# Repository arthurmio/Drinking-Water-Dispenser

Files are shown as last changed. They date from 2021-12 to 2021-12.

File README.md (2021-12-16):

# Drinking Water Dispenser
The objective of the project is to build a paid water dispenser to fill 1L bottles.

This dispenser will be located on the roadside to allow hikers to recharge their bottle and thus reduce the use of plastic.

The project is developed by Mandor which is an ecological reserve located 4km from the village of Machu Picchu in Peru, 
possessing a botanical garden with a waterfall to discover the flora and fauna, a restaurant, accommodation and a campsite.

# Contact
Facebook / Instagram : @mandormachupicchu

Whatsapp : +51 940 188 155

<p align="center">
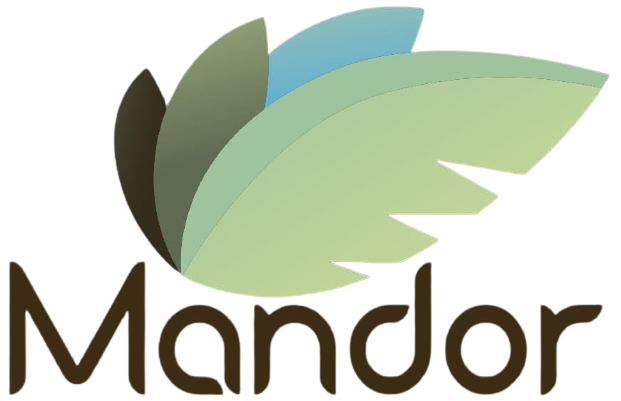
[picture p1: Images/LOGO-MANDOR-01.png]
mandor logo
  
</p>

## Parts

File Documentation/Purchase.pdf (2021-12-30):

Name | Component | Reference Naylamp | Price (soles) | Url
Coin Acceptor Selector de monedas CH-926 #SKU: 000373 140 https://naylampmechatronics.com/sensores/373-selector-de-monedas.html
Flow Meter Sensor de flujo de agua 1/2" YF-S201 #SKU: 000108 20 https://naylampmechatronics.com/sensores-liquido/108-sensor-de-flujo-de-agua-12-yf-s201.html

Solenoid Valve Válvula solenoide 1/2" 12VDC #SKU: 000314 25 https://naylampmechatronics.com/valvulas/314-valvula-solenoide-1p2-pulg-12vdc.html

Button Pulsador con cubierta #SKU: 000211 1 https://naylampmechatronics.com/accesorios-y-prototipado/211-pulsador-con-cubierta-para-kit.html

Arduino Arduino Nano Every with Headers / 61 https://store-usa.arduino.cc/collections/boards?sort_by=price-ascending

Relay or Transistor 12V DRIVER MOSFET IRF520 6A #SKU: 000239 6 https://naylampmechatronics.com/drivers/239-driver-mosfet-irf520-6a.html
DC-DC Converter Convertidor Voltaje DC-DC Step-Up 2A MT3608 #SKU: 000119 15 https://naylampmechatronics.com/conversores-dc-dc/119-convertidor-voltaje-dc-dc-step-up-2a-mt3608.html
/!\ Complementary material Resistance Capacity Led Cables BreadBoard Multimeter Arduino Alimentation | TOTAL 268

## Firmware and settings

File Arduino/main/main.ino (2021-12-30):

//////////////////////////////////////////////////////////////////////////
/// Name        : main.ino
/// Description : Principal code for drinking water dispenser
/// Author      : Arthur MARIANO
/// Github      : https://github.com/arthurmio/Drinking-Water-Dispenser
/// Date        : 27/12/2021
//////////////////////////////////////////////////////////////////////////

#include <Arduino.h>
#include <Time.h>

///////////////////
// Instantiation //
///////////////////

// Time //
volatile float currentTime = 0.00;
volatile float lastTime = 0.00;
volatile float start = 0.00;
volatile float coinsValueSavedTime = 0.00;

// Flow Meter //
const int flowMeterPin = 2; // interrupt port
const float factorK = 7.5;
volatile int pulse_freq = 0 ;
volatile float flow = 0.00;
volatile float waterVolume = 0.00;
volatile float flowCounter = 0.00;

// Coin Acceptor //
const int coinAcceptorPin = 3; // interrupt port
volatile float coinsValue = 0.00;
volatile float coinsValueSaved = 0.00;
volatile float moneyValue = 0.00;
volatile bool payed = false;

// Solenoid //
const int solenoidPin = 4; 


///////////
// setup //
///////////
void setup() {
  pinMode(flowMeterPin, INPUT);
  pinMode(coinAcceptorPin, INPUT); 
  pinMode(solenoidPin, OUTPUT);
  Serial.begin(9600);
  attachInterrupt(digitalPinToInterrupt(flowMeterPin), pulseFlow, RISING);
  attachInterrupt(digitalPinToInterrupt(coinAcceptorPin), pulseMachine, RISING);
  currentTime = millis();
  lastTime = currentTime;
}


//////////
// loop //
//////////
void loop(){
  // money calcul
  currentTime = millis();
  if(currentTime <= (start+1000)){
    coinsValueSaved = coinsValue;
    coinsValueSavedTime = millis();
  }
  else{
    coinsValue = 0;
  }
  if(currentTime >= (coinsValueSavedTime+1000)){
    if(coinsValueSaved>=5 && coinsValueSaved <= 11){
      moneyValue = 1; // 0.50 sole
      solenoidOpen(moneyValue); 
    }
    else if(coinsValueSaved>11){
      moneyValue = 2; // 1 sole
      solenoidOpen(moneyValue);
    }
    else{
      moneyValue = 0; // no money
      solenoidOpen(moneyValue);
    }   
  }
  flowCounter=0.00;
  flow=0.00;
  pulse_freq=0.00;
  while(payed==true){
    currentTime = millis();
    if(currentTime >= (lastTime + 100)) // count always the flow every second 
    {   
      lastTime = currentTime; 
      flow = (pulse_freq / factorK) / 60; // flow in L/min
      pulse_freq = 0; // Reset Counter
      Serial.print(flow, DEC); 
      Serial.println(" L/Min");
      flowCounter = flowCounter + flow;
      Serial.print(flowCounter, DEC); 
      Serial.println(" L");
      flowCount(moneyValue, flowCounter);
      digitalWrite(solenoidPin, LOW); // solenoid open
    }
  }
  digitalWrite(solenoidPin, HIGH); // solenoid closed
}

///////////////
// Functions //
///////////////

// Flow Meter //
void pulseFlow() // interrupt fonction for flow meter
{
  pulse_freq++;
}

void flowCount(int moneyValue, float flowCounter){ // calcul for volume
  if(moneyValue == 1){
    if(flowCounter >= 0.50){
      payed = false;
      Serial.println("0.50L water served");
    }
  }
  else if(moneyValue == 2){
    if(flowCounter >= 0.97){
      payed = false;
      Serial.println("1L water served");
    }
  }
  coinsValueSaved=0;
}

// Coin Acceptor //
void pulseMachine(){ // interrupt fonction for coin acceptor
  coinsValue  = coinsValue + 0.5;
  start = millis();
}

// Solenoid //
void solenoidOpen(int moneyValue){
  if(moneyValue==1){ // 0.50sole
    payed = true;
  }
  else if(moneyValue==2){ // 1sole
    payed = true;
  }
  else
    payed = false;
}

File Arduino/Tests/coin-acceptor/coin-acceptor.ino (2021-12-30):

//////////////////////////////////////////////////////////////////////////
/// Name        : coin-acceptor.ino
/// Description : Code for testing the coin-acceptor CH-926
/// Author      : Arthur MARIANO
/// Github      : https://github.com/arthurmio/Drinking-Water-Dispenser
/// Date        : 30/12/2021
//////////////////////////////////////////////////////////////////////////
#include <Arduino.h>
#include <Time.h>

//Time
volatile float currentTime = 0.00;
volatile float lastTime = 0.00;
volatile float start = 0.00;
volatile float coinsValueSavedTime = 0.00;

const int coinAcceptorPin = 3;
volatile float coinsValue = 0.00;
volatile float coinsValueSaved = 0.00;


void setup() {
  pinMode(coinAcceptorPin, INPUT); 
  Serial.begin(9600);
  attachInterrupt(digitalPinToInterrupt(coinAcceptorPin), pulseMachine, RISING);
  
}

void loop() {
  currentTime = millis();
  if(currentTime <= (start+1000)){
    coinsValueSaved = coinsValue;
    coinsValueSavedTime = millis();
  }
  else{
    coinsValue = 0;
  }
  if(currentTime >= (coinsValueSavedTime+1000)){
    if(coinsValueSaved>=5 && coinsValueSaved <= 11)
      Serial.println("0.50 soles");
    else if(coinsValueSaved>11)
      Serial.println("1 soles");
  }
}

void pulseMachine() // interrupt fonction for coin acceptor
{
  coinsValue  = coinsValue + 0.5;
  start = millis();
}

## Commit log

2021-11-27 First Arduino file
2021-12-16 Schematics without change machine make with fritzing
    [Schematics_without_change_machine.fzz]
2021-12-16 Arduino tests files for each component
2021-12-26 Tests code changed and verified with material
2021-12-27 First version of main without solenoid
2021-12-29 Version 1.0 of the main project
    [Schematics_without_change_machine.fzz]
2021-12-30 Rename 'change machine' with 'coin acceptor'
    [Schematics_without_coin_acceptor.fzz]
2021-12-30 Correction to the schematics without coin acceptor
    [Schematics_without_coin_acceptor.fzz]
